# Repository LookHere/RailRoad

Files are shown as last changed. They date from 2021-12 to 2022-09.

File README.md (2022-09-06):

# RailRoad

Many model railroad enthusiasts have basements filled with photo-realistic layouts or join clubs with amazing cities and yards. I’m not an enthusiast, but a few years ago I pulled out an old Lionel set I had as a kid and thought a new paint job could make it look less plasticy. I’ve never built a layout (nor would I have room for a large one) but occasionally I’d send a train around a loop or paint a few figures.

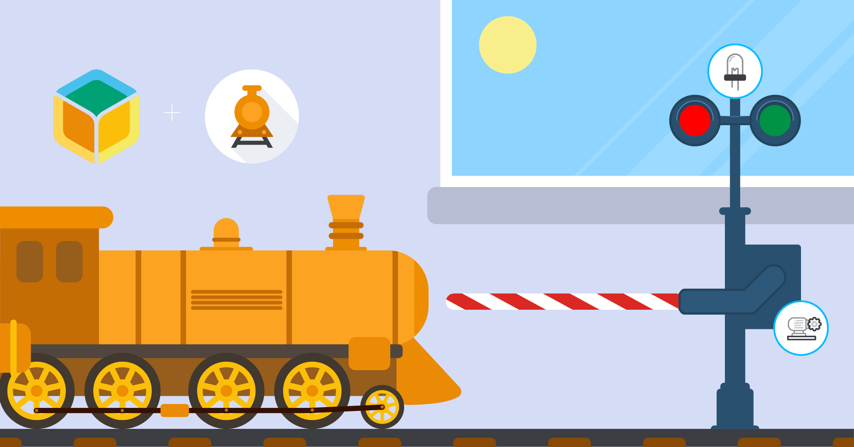
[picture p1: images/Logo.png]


Although I’ve never worked with Raspberry Pi, servos, resistors or done much coding, the balena platform made it easy to get started. It also makes it easy to add and manage additional devices when I’m ready to expand my setup. Although building my first scene still took some effort, I’m happy with the final results (see video at the end).

## Part of the balenaLabs Residency Projects

Every new balenista starts their journey by creating a project as [part of their onboarding](https://www.balena.io/blog/balenalabs-residencies-our-quest-to-improve-onboarding-at-balena/). This project guide is my reflection of my own residency, allowing me to meet new teammates, get to know the platform, and understand how our users put balena products to work.

To learn more about this unique opportunity, see my article ["How We Craft an Entirely Different Onboarding Experience"](https://www.linkedin.com/pulse/how-we-craft-entirely-different-onboarding-experience-john-kelly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).

## The Scene

I thought it would be fun to think about a specific time and location to ground the model in history. I decided the scene should be on October 31st of 1873 near the Kissena Lake stop of the [Central Railroad of Long Island](https://en.wikipedia.org/wiki/Central_Railroad_of_Long_Island).

The farming community would have celebrated Halloween largely as a festival of the harvest, coming together at large banquites. Although it only ran from 1871 to 1874, the The Central Railroad of Long Island started a transformation in the community, from rural farmland into what would eventually be part of urban New York City.

## Project overview

The center of the operation is a Raspberry Pi running balenaOS and connected to balenaCloud. That way I can flash the device once (using balenaEtcher) and then easily update the code via wifi, making changes in the cloud and never having to take out the SD card again (something that’ll be very helpful if the pi is installed in a layout).

I wanted the project to be robust, but also easy to assemble and change. I started laying out the parts on a breadboard, and then once I was satisfied with my circuit design, I soldered all the parts to a Perma-Proto PCB. That board was then connected to the Raspberry Pi GPIO pins via screw terminals on a HAT.

# Tutorial

## Hardware required

Most of the basic parts were from the CanaKit Pi 4 Ultimate Kit, which was a good way to start. Each action only needed one additional item: the chicken needed a servo, the lighting needed LEDs, and the sound needed an audio output. The only tools I needed were a soldering iron (with some wire, lead, & flux) and a screwdriver (with some screws).

- Raspberry pi 4 - [CanaKit Raspberry pi 4 2GB Ultimate Maker Kit](https://www.microcenter.com/product/611946/canakit-raspberry-pi-4-2gb-ultimate-maker-kit)
- SD card
- Screw Terminal Hat - [52Pi RPi GPIO Screw Terminal Hat](https://www.microcenter.com/product/632047/52pi-rpi-gpio-screw-terminal-hat)
- Circuit Board - [Adafruit Perma-Proto Half-sized Breadboard PCB](https://www.adafruit.com/product/571)
- Power adaptor for the circuit board - [5V 2A (2000mA) switching power supply](https://www.adafruit.com/product/276)
- Power connection - [Breadboard-friendly 2.1mm DC barrel jack](https://www.adafruit.com/product/373) ([spec sheet](https://cdn-shop.adafruit.com/datasheets/21mmdcjackDatasheet.pdf))
- Continuous Rotation Servo - [FeeTech FS5103R](https://www.adafruit.com/product/373) ([spec sheet](https://media.digikey.com/pdf/data%20sheets/adafruit%20pdfs/154_web.pdf) and [more spec sheet](https://www.pololu.com/file/0J1433/FS5106R-specs.pdf))
- Position Based Servo - [MCM Electronics TowerPro SG-5 Standard Servo](https://www.microcenter.com/product/454407/mcm-electronics-towerpro-sg-5-standard-servo)
- Speaker connection - [USB Audio Adapter](https://www.adafruit.com/product/1475)
- Lights - [Evil Mad Science Candle Flicker LED Assortment - 15 Piece](https://www.microcenter.com/product/453261/evil-mad-science-candle-flicker-led-assortment-15-piece)
- Buttons - [16mm Illuminated Pushbutton](https://www.adafruit.com/product/1439)

## Tools and materials

- Soldering Iron - [Aven Soldering Iron with Fine Tip - 40W](https://www.microcenter.com/product/442727/aven-soldering-iron-with-fine-tip-40w) (this is a [great beginner tutorial on soldering](https://learn.adafruit.com/adafruit-guide-excellent-soldering/tools))
- Solder 60/40 - [Rosin Core - 0.5mm/0.02" diameter - 50 grams](https://www.adafruit.com/product/1886)
- Connections (to easily plug in servos and lights) - [Extra-long break-away 0.1" 16-pin strip male header (5 pieces)](https://www.adafruit.com/product/400)
- Wire - [Hook-up Wire Spool](https://www.adafruit.com/product/1311)
- Screwdriver and screws
- Speakers to play the audio output

## Software required

- You’ll need a [balenaCloud account](https://dashboard.balena-cloud.com/signup) – remember: your first ten devices are free and fully-featured!
- The code for this project is available [on balenaHub](https://hub.balena.io/organizations/johnkellyiv/projects/RailRoad)
- Use a tool like [Etcher](https://www.balena.io/etcher/) to flash the OS image onto your SD card
- You can also [download balenaCLI](https://github.com/balena-io/balena-cli) if you want to get into the nitty-gritty of device management via command line

# Assembly
My project looks very specific to my individual use case, but I mainly want to show how someone can start automating motors and LEDs with balena. You can take this in any direction you want, or just replicate your own version of what I’ve built.
It all starts with creating your balenaCloud account and clicking this button to add this project as a Fleet within your dashboard:

[Deploy with balena](https://dashboard.balena-cloud.com/deploy?repoUrl=https://github.com/LookHere/RailRoad)

The entire project was written in python and can be found [here on GitHub](https://github.com/LookHere/RailRoad/tree/main/controller). The docker-compose.yml sets up the different containers. 

In the Controller directory, the Dockerfile installs the libraries and copies over the code and sound files. The trigger.py is all of the code that runs the servo, light, sound, and buttons. The last command in the Dockerfile runs the trigger.py code upon startup.

When prototyping on the breadboard, it was important to know how to connect the Raspberry Pi 4 to everything else. This [GPIO pinout](https://www.etechnophiles.com/raspberry-pi-4-gpio-pinout-specifications-and-schematic/) really helped. There is a lot of information on [how to use each pin](https://www.etechnophiles.com/raspberry-pi-4-gpio-pinout-specifications-and-schematic/). Once I moved off of the breadboard and onto the screw terminal hat, it became much easier since small LEDs indicated what was active (though there was some confusion for [pins with multiple names](https://roboticsbackend.com/raspberry-pi-3-pins/), like “pin 9” called “MISO”). I used [raspberry-gpio-python](https://sourceforge.net/p/raspberry-gpio-python/wiki/Examples/), a python module to control the GPIO pins on a Raspberry Pi.

The servo was by far the most difficult to work with. [Wiring it up](https://docs.arduino.cc/learn/electronics/servo-motors) was easy. Understanding the basics of the [duty cycle](https://www.digikey.com/en/maker/blogs/2021/how-to-control-servo-motors-with-a-raspberry-pi) wasn’t that bad (though it is interesting how much it’s [used in different ways](https://en.wikipedia.org/wiki/Duty_cycle)). The challenge came in figuring how to send the correct length pulse to get the movement expected.

## Chicken action challenges
The original concept was to have a chicken come out of a chicken coop, move back and forth for a while, and then go back into the coop. I knew it would be possible to do this with electronics or by manually manipulating a stick (like a puppet), but by using software-controlled hardware it would be a lot easier to upgrade this action later, like to coordinate with a day/night cycle or to run away when a train was passing by. The first thing I did was to use household scraps to build a physical proof of concept to make sure that the action made sense. One side mimicked the rotation of the servo to move a wooden skewer while the other side moved the chicken out of the coop. 



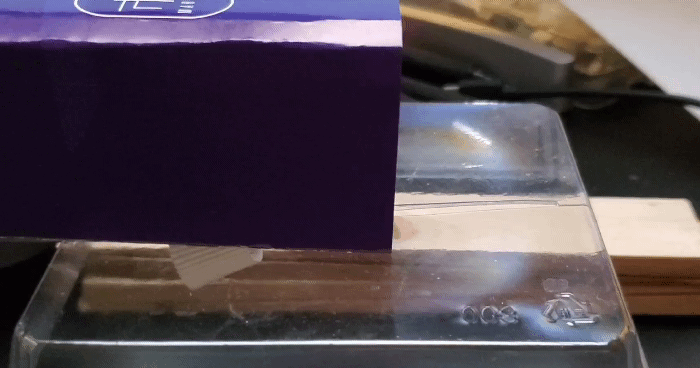
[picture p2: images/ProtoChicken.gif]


Next I had to build the chicken action. I used a Raspberry Pi 4, which is a bit overpowered for this role, but I wanted to have the resources ready to keep building on top of this foundation. I used a CanaKit bundle since it came with the wires, resistors, LEDs, etc. that I needed (full parts list below).
I learned SketchUp to design a yoke to keep the rod moving in a lateral direction, even though the servo was rotating in a circle. It was mainly just four holes for screws to connect it to the layout and a long, center channel to make sure the rod only moved forward and backwards. As long as I only use around ninety degrees on one side of the servo, I estimated that the yoke would be enough to keep the rod moving in the right direction.

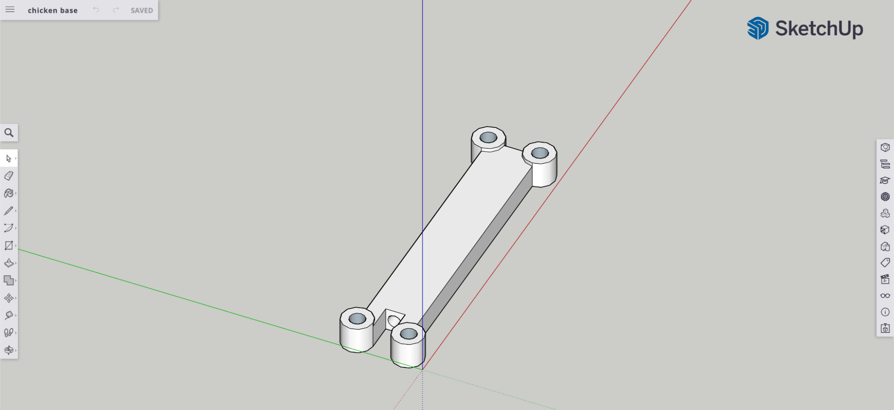
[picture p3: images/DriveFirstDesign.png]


Next I needed a servo to transfer the electrical signal into an action. I chose the FeeTech FS5103R continuous rotation servo. I learned a lot about how sending different length pulses would move a continuous rotation servo clockwise or counterclockwise at various speeds. I set up the timing to move the chicken out of the coop, rock around outside, and then move back into the coop. Since the servo is based on speed, I had to make sure the amount of travel out of the coop equaled the amount back into it.

After working that out I tested it and got inconsistent results. I believe the small, quick movements of rocking the chicken around weren’t consistently being registered so it would occasionally not come back to the home position. This was especially bad for the engineering, since rotating a full 360 degrees would bring the rod so far from its expected path that it may break.

Then I tried to go with a position based servo, where sending a signal would tell it a location, not a speed/direction. I used the TowerPro SG-5 Standard Servo and rewrote the code. I wasn’t happy with Sketchup so I taught myself Blender to design a [Scotch yoke](https://en.wikipedia.org/wiki/Scotch_yoke), which I thought was safer if the servo did ever go further than expected or if I wanted to ever use the continuous servo for a lateral motion. I created a tapered hole in one end to wedge the stick in and an indented surface for more surface area for the hot glue to stick to.

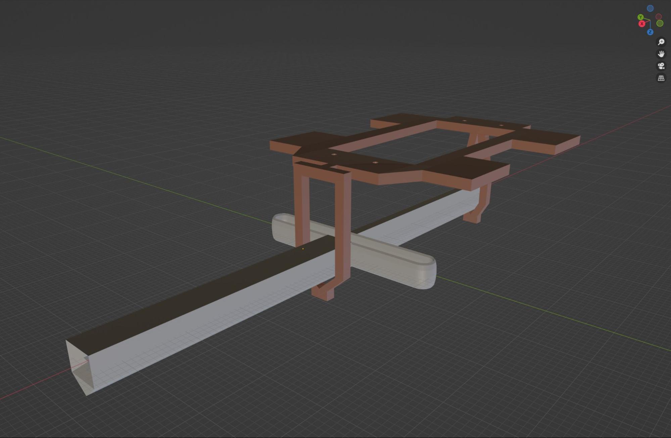
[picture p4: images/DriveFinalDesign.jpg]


This new servo didn’t move enough, so I went back to the original continuous servo, but used the Scotch yoke. It’s still inconsistent, but I’m going to keep working with the code to try to improve it in the future.

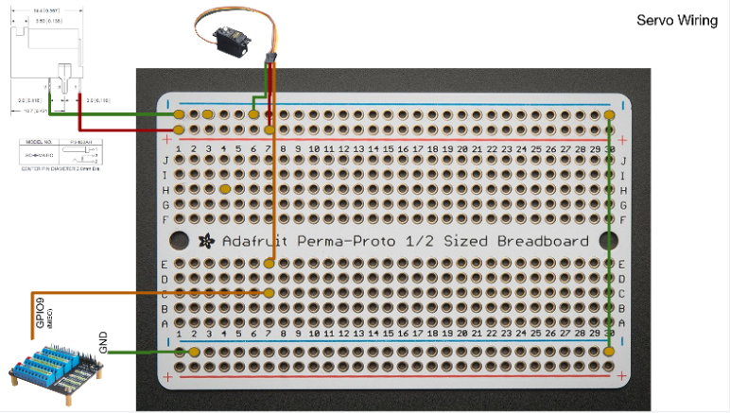
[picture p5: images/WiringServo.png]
 
 
## Lighting
 
The basic idea was for the lighting to turn on and off using a switch. I wanted the switch to send a signal to the Raspberry Pi, and for the Pi to send a signal to the LED. That way later we can upgrade the system and connect the lights to a day/night cycle and other more complex actions.

This scene takes place before the Edison Electric Illuminating Company began electrifying Manhattan in 1882 (and well before electricity reached the Eastern Queens building I’m modeling). The lighting in the area may have been from whale oil or kerosene, but I’m modeling candles here since I wanted the lights to flicker. Although we could have flickered the LED by turning it on and off quickly, it was easier just to buy LEDs that flickered on their own. 
  
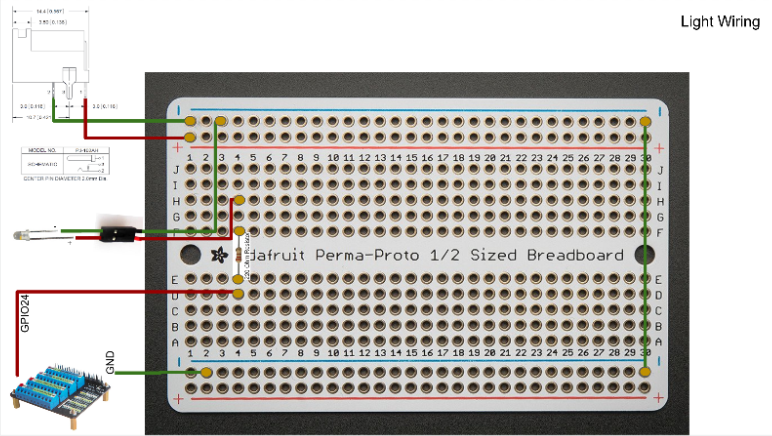
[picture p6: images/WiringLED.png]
 
 
## Sounds

To simplify the sound, I used a USB Sound Adaptor. One end plugged into a USB on the Raspberry Pi and the other side had a normal speaker jack.
One of the benefits of building this on balena is the ability to use “balenaBlocks”, pre-written segments of code ready to use in an application. I was very happy to see an [audio block](https://github.com/balenablocks/audio), so most of the challenging coding was already done. This block runs a PulseAudio server optimized for balenaOS and helps route audio from a source to a sink. I decided to use [pydub](https://pythonbasics.org/python-play-sound/) as the audio source in my Python application since it didn’t require much coding or many libraries.

The original sound was in the .mp3 format, but that wasn’t working well so I found one in .wav format. After getting the file into the container and adding the code into my Python program, the audio worked great. I set up the file to play a chicken sound in the middle of the chicken movement.

## Buttons

I could trigger the actions in different ways, but I thought physical buttons would be a good start. The buttons have four terminals; two of the leads are used to power the internal LED and two of the leads complete the circuit when the button is pressed. The buttons are considered “momentary” in that the connection is only made when the button is pushed (in comparison to other buttons that stay on or off after they are pushed). I connected these directly to the screw terminal hat, just so they are easier to install.

I designated one button to turn the light on and off. The other button triggers an action where the chicken leaves the coop, makes a sound, and then goes back into the coop. As I build out the layout, I hope to add more buttons that generate more advanced actions. I think adding this interactivity makes the scene more engaging.
 
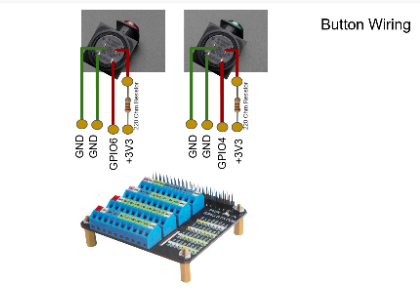
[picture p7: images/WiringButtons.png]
 

# Here's a fun demo of things working

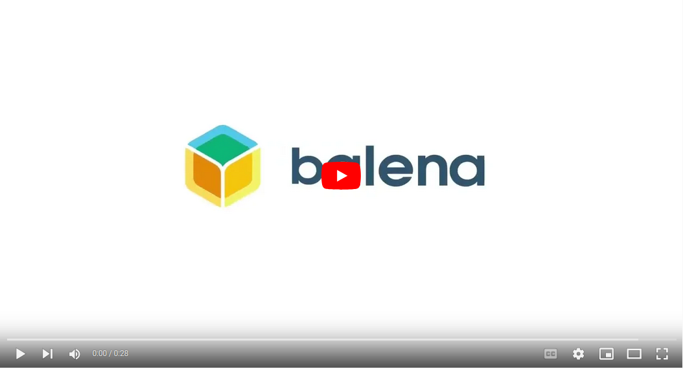
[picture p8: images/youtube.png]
Watch the video (https://www.youtube.com/watch?v=yKxnS1Gk3TE)


With my particular hardware and setup, here's how I got some automation going for my train scene. Yours will vary, and you might even change up a ton of the code. Your literal mileage may vary here.

# Future work
I started with the chicken scene because I thought it was the easiest action I could put together, while still being a building block for more complex work. I’d like to create more ways to interact, including being able to trigger events from a button on a webpage and to create a script to have different actions timed in more complex ways. Since this is all running on balenaCloud, pushing out new code to the device is incredibly easy.

These same techniques can be used for a wide variety of different animations. I’d love to have a festive party with apple bobbing and a halloween seance with levitating candelabras. This system could make it easy to coordinate the classic “house on fire” scene, since the smoke, lights, and sounds can all be linked to a central control mechanism and triggered on a script.

I’ve seen some [great work by others](https://www.jmri.org/) in managing train operation with [DCC](https://www.nmra.org/dcc-working-group). As a layout grows and new trains are added, having an easy way to update devices could save a lot of time. I could imagine balena being really useful for shared club layouts, where devices could easily have new software added anywhere - while on the layout or while the club member is working on it in their own attics and basements. Having a networked connection will ensure that everything works well when brought together.

There are also some projects used in other areas that might be easily transferred to model trains. The [Inky pHAT](https://www.balena.io/blog/send-personal-messages-and-inspirational-quotes-with-this-e-ink-display-project/) is an e-paper display that could be used as a train bulletin board, identifying the schedule of the day. It would be cool to pair this with an[ object detection algorithm](https://www.balena.io/blog/build-an-ai-driven-object-detection-algorithm-with-balenaos-and-alwaysai/), so a camera can identify the train by sight and then alert the station bulletin board which train is approaching. Since many cities give out their operating data, not only would it be possible to [display train times](https://www.balena.io/blog/build-a-raspberry-pi-powered-train-station-oled-sign-for-your-desk/), but also run a model layout that exactly mirrors what is happening live.

What’s most interesting to me though, is how we can use these devices to make railroad challenges. For much of railroading history, different controllers (switches, components, trains, dispatchers, etc.) didn’t have a method to talk to each other. To mirror the real world in a model train layout, instead of controlling everything at the same terminal, we could write some logic to make a few cheap pi zeros act like independent agents.

For example, an independent controller could manage the car/bike traffic in a town and only stop if the level crossing signals are triggered early enough. Or the logic of signaling (before centralized traffic control) could be managed by independent pi zeros, each one controlling an automatic block signaling system according to pre-programed rules. By creating world logic, it gives us the same limited information and control of the conductors at the time. Although these devices would be designed not to talk to each other (since they wouldn’t in the real world), their software would all be easily updated over wifi, making it easy to develop, maintain, and upgrade. Coordinating train traffic in a world of independent variables could create some really realistic and challenging layouts.

This was my exploration of a few spaces I have very little experience in. I hope you share what you’re working on or what you’d like to work; there is a lot of fun that could be had with the tools we already have access to.

# Technical Details
If you're looking to recreate this project for yourself, here are more of the technical details.

## Model Railroad Controller

- Input GPIO 4 = LED button
- Input GPIO 6 = chicken button
- Out GPIO 24 = candle LED
- Out GPIO 18 = servo 1 (Continuous rotation)
- Out GPIO 9 = servo 2 (position based)

Utilizes [raspberry-gpio-python](https://sourceforge.net/p/raspberry-gpio-python/wiki/Examples/) to access the GPIO pins.

## Overall Wiring diagram
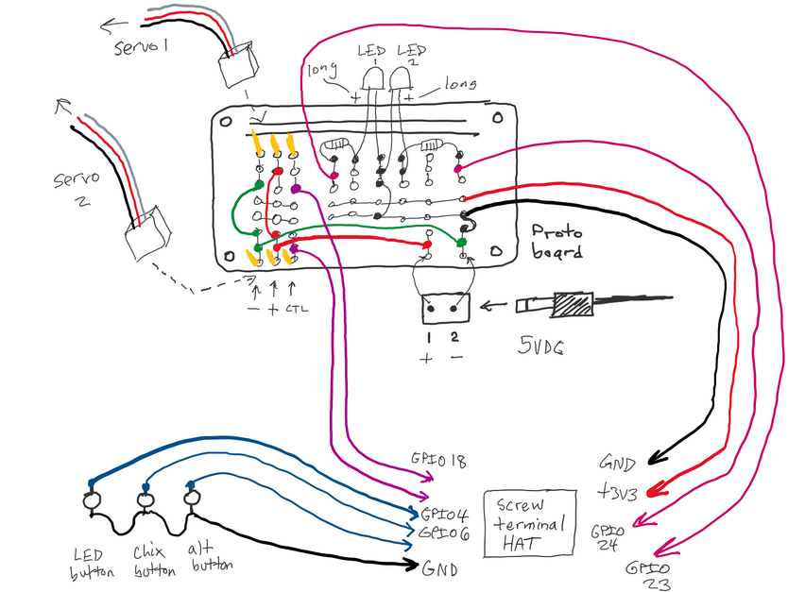
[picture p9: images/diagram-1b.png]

(See https://www.digikey.com/en/maker/blogs/2021/how-to-control-servo-motors-with-a-raspberry-pi)

To wire the servo: 
- The white (or yellow) wire is connected to the signal.  
- The red (or orange) is connected to the 5 volt power. 
- The black (or brown) is connected to ground.  

We set this program to a frequency of 50 hertz.
Milisecond is 1,000th of a second.

## Continuous Rotation Servo 
The first servo was the continuous rotation servo - FeeTech FS5103R.  That didn't work for the chicken movement, but could still be good for other future applications.

Unlike other servos that that rotate to a position, this servo rotates backwards or forwards:
- 1.0ms pulse - Full Speed Clockwise 
- 1.5ms pulse - Stop
- 2.0ms pulse - Full Speed Counter Clockwise
 
For this servo, we used GPIO 18 to control the movement.

### Servo datasheet
https://media.digikey.com/pdf/data%20sheets/adafruit%20pdfs/154_web.pdf

### Servo coding examples
https://www.instructables.com/Servo-Motor-Control-With-Raspberry-Pi/

https://www.teachmemicro.com/raspberry-pi-pwm-servo-tutorial/

## Position Based Servo
The second servo we used was a standard servo - MCM Electronics TowerPro SG-5.  

This servo used pulses to move to specific locations
- 1.0ms pulse - Full Left, -90 degree position  
- 1.5ms pulse - Middle, 0 degree position 
- 2.0ms pulse - Full Right, 90 degree position 

For this servo, we used GPIO 9 (also known as miso) to control the movement.

### Servoc coding examples
https://www.arduino.cc/en/Tutorial/LibraryExamples/Sweep

## Lighting
The long side for LED connects to the positive (red wire), then to a 220 Ohm Resistor, and then to GPIO 24.  The short side connects to the ground (green wire).

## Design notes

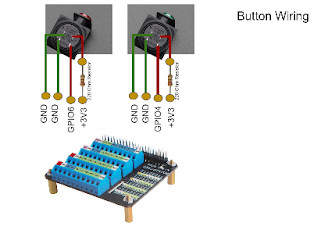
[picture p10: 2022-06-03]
images/Button.jpg

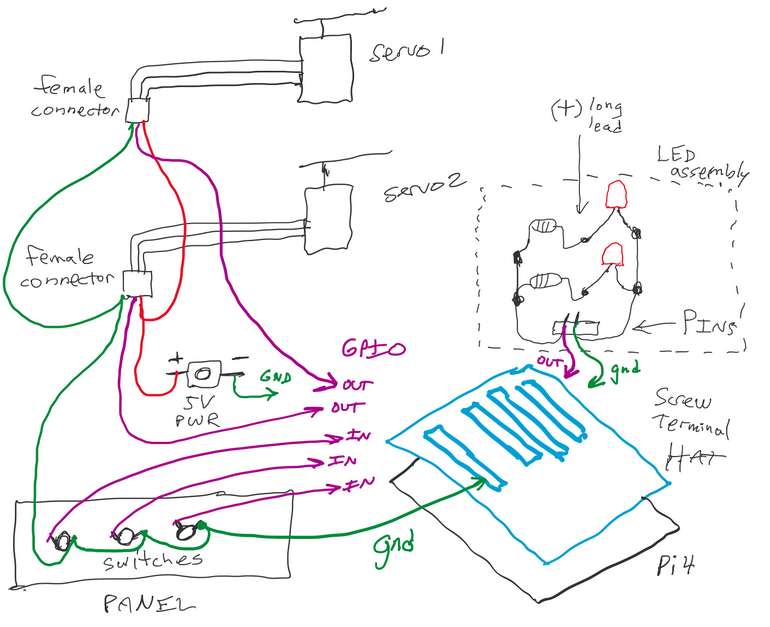
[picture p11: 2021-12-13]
images/diagram-1a.png

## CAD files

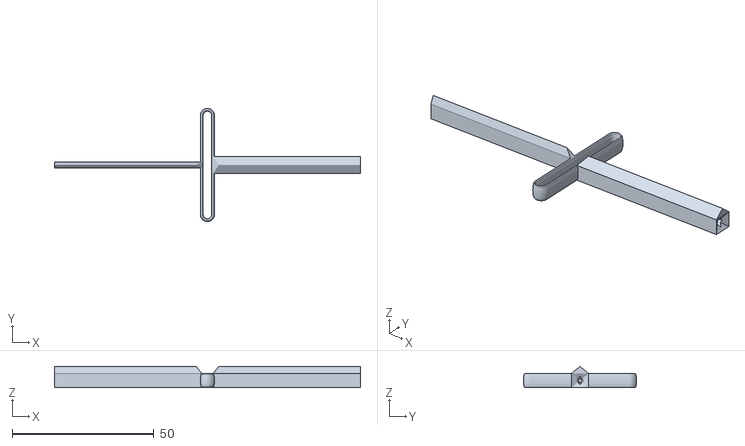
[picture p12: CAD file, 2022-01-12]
3dPrints/YokeOnly09.stl
108.1 x 40.0 x 7.50

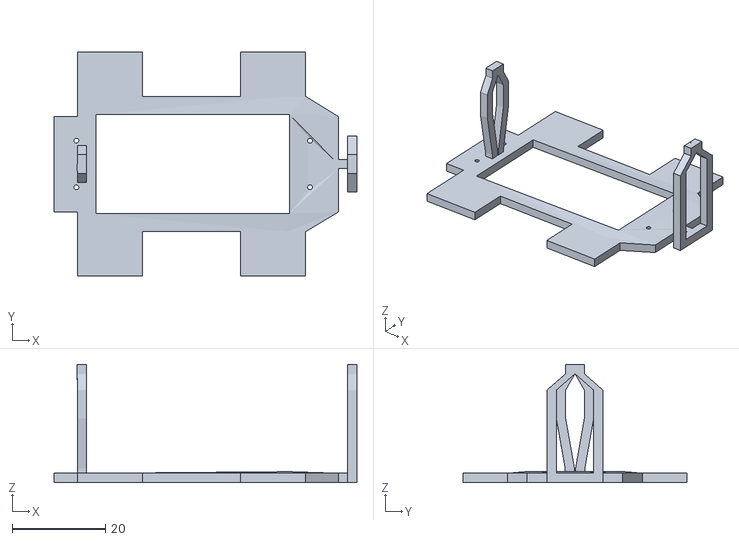
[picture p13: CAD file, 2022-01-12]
3dPrints/SupportOnly09.stl
65.0 x 48.0 x 25.3

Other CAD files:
3dPrints/ScotchYoke09.blend

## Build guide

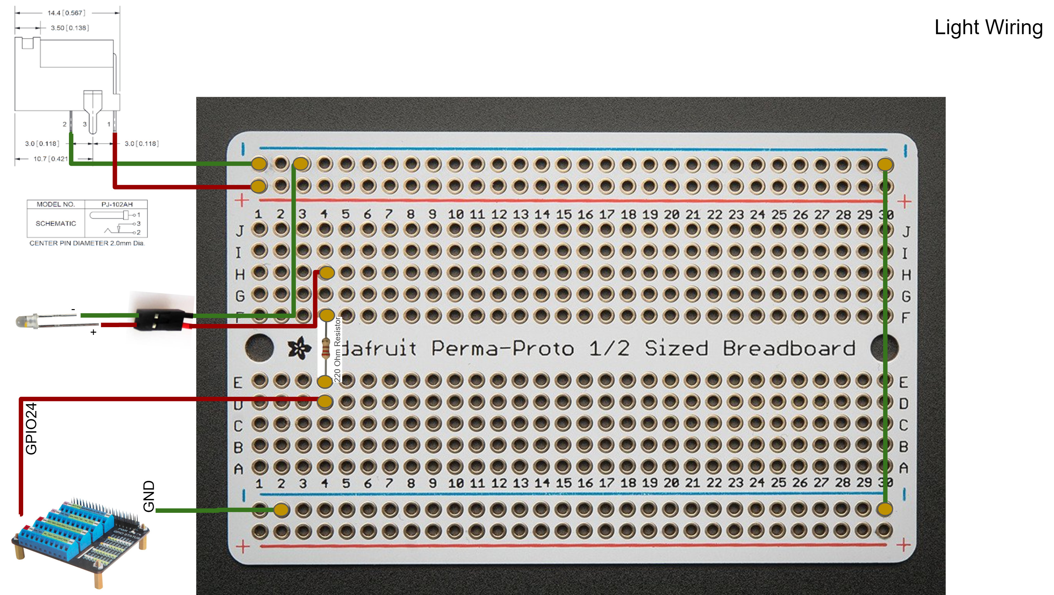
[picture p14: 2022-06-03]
images/LightingWiring.jpg

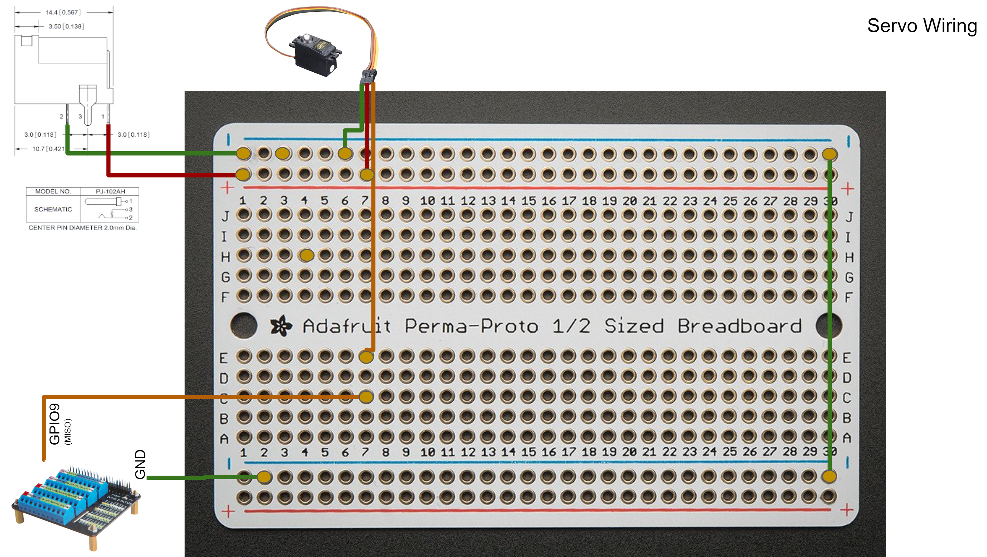
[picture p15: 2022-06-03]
images/ServoWiring.jpg

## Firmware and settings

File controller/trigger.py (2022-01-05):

import time
import datetime
import RPi.GPIO as GPIO
import os
from pydub import AudioSegment
from pydub.playback import play

#song = AudioSegment.from_wav("sound.wav")
#play(song)

GPIO.setmode(GPIO.BCM)

# Callback functions that execute when GPIO values change:
def button_led(channel):
    #
    # Detects LED button press
    #
    print("LED button pressed!")
    # Set the LED to be opposite its current value:
    GPIO.output(24, not GPIO.input(24))

def button_chicken(channel):
    #
    # Detects chicken button press
    #
    print("Chicken button pressed!")
    chicken_move()

def chicken_move():
    global p

#SetAngle method of movement
#    SetAngle(50)
#    SetAngle(22)
#    SetAngle(100,0.5)

#SetServoPercent method of movment
#    zero is full reverse
#    50 is stop
#    100 is full forward
    """
    SetServoPercent(50,1) #come out
    print("chicken comes out")
    #SetServoPercent(40,2) #pause

   # for x in range(10):
   #      SetServoPercent(30,0.5) #jimmy back
   #      SetServoPercent(50,0.5) #jimmy forward
   #      print("jimmy")

    SetServoPercent(30,1)  #back home
    print("chicken goes back")


    print("Chicken movement done!") 
    """

#Position based movement
    print("chicken move start")
    p.ChangeDutyCycle(1.5)
    print("1.5")
    time.sleep(0.5)
    """p.ChangeDutyCycle(3)
    print("6.5")
    time.sleep(1)
    p.ChangeDutyCycle(5)
    print("7")
    time.sleep(1)
    p.ChangeDutyCycle(7.5)
    print("7.5")
    time.sleep(1)
    p.ChangeDutyCycle(10)
    print("8")
    time.sleep(1)
    """
    p.ChangeDutyCycle(0)
    print("0")
    time.sleep(0.5)
    play(AudioSegment.from_wav("chicken2.wav"))
    time.sleep(0.5)
    p.ChangeDutyCycle(25)
    print("25")
    time.sleep(0.5)
    p.ChangeDutyCycle(0)
    print("0")
    time.sleep(0.5)
    print("chicken end")


#code for position servo
def SetAngle(angle, dur=1):
    duty = angle / 18 + 2
    GPIO.output(9, True)
    p.ChangeDutyCycle(duty)
    time.sleep(dur)
    GPIO.output(9, False)
    p.ChangeDutyCycle(0)

#code for continuing servo
def SetServo(duty, dur=1):
    GPIO.output(9, True)
    p.ChangeDutyCycle(duty)
    time.sleep(dur)
    GPIO.output(9, False)
    p.ChangeDutyCycle(0)


#code for position servo that is scaled up
def SetServoPercent(duty, dur=2):
    scaler = make_interpolater(0, 100, 5, 10)
    GPIO.output(9, True)
    print("scaler {} ".format(scaler(duty)))
    p.ChangeDutyCycle(scaler(duty))
    time.sleep(dur)
    GPIO.output(9, False)
    p.ChangeDutyCycle(0)


def make_interpolater(left_min, left_max, right_min, right_max):
    #
    # Scales one range to another...
    # Function that returns a function (closure)
    # see https://stackoverflow.com/questions/1969240/mapping-a-range-of-values-to-another
    #

    # Figure out how 'wide' each range is  
    leftSpan = left_max - left_min  
    rightSpan = right_max - right_min  

    # Compute the scale factor between left and right values 
    scaleFactor = float(rightSpan) / float(leftSpan) 

    # create interpolation function using pre-calculated scaleFactor
    def interp_fn(value):
        return right_min + (value-left_min)*scaleFactor

    return interp_fn





"""

servoPIN = 9
GPIO.setup(servoPIN, GPIO.OUT)

p = GPIO.PWM(servoPIN, 50) # GPIO 9 for PWM with 50Hz
p.start(2.5) # Initialization
try:
  while True:

except KeyboardInterrupt:
  p.stop()
  GPIO.cleanup()
"""


# Define the GPIO pins we'll be using:

# LED Input:
GPIO.setup(4, GPIO.IN, pull_up_down=GPIO.PUD_UP)
GPIO.add_event_detect(4, GPIO.RISING, callback=button_led, bouncetime=200)

# Chicken Input:
GPIO.setup(6, GPIO.IN, pull_up_down=GPIO.PUD_UP)
GPIO.add_event_detect(6, GPIO.RISING, callback=button_chicken, bouncetime=200)

# LED  Output:
GPIO.setup(24, GPIO.OUT)

# Chicken Output:
GPIO.setup(9, GPIO.OUT)

# Set the initial output values
GPIO.output(24, GPIO.HIGH)
p = GPIO.PWM(9, 50)
p.start(0)

try:
    while True:
        time.sleep(5)
except KeyboardInterrupt:
    print("Interrupted!")
    p.stop()
    GPIO.cleanup()

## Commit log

2021-12-13 Add servo movements
2021-12-14 added servo information
2021-12-14 more servo math
2021-12-14 updated servo
2021-12-28 setting up second servo
2021-12-28 more second servo data
2021-12-31 cleaned up cont. rotation servo section to match position servo
2021-12-31 soldering file v3
2022-01-03 servo colors
2022-01-03 more fine tuning of how the servo's work
2022-01-12 description of stl files
2022-06-03 Adding wiring diagrams
